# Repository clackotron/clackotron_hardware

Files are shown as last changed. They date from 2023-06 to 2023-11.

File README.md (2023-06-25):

# Clackotron 2000 - Hardware
This repository contains the hardware for the Clackotron 2000 project, which provides a simple, all-in-one solution for controlling SBB split-flap modules. For more information on the project in general, visit the [docs repository](https://github.com/clackotron/clackotron_docs).

The hardware is based around an ESP32-S3 and designed in KiCAD 7.0. The production files can be used to easily order the latest version of the PCB from a manufacturer. (JLCPCB)

Most notably, the hardware contains:
* 30V DC input and +/-/A/B connector (same as SBB split flap modules).
* Internal power supply for 5V (RS485) and 3.3V (ESP32-S3).
* An ESP32-S3 on which the [firmware](https://github.com/clackotron/clackotron_firmware) and [webinterface](https://github.com/clackotron/clackotron_webinterface) will run.
* A level converter for sending/receiving RS485 from the ESP32-S3.
* An RTC (PCF85263A) and battery for time-keeping while offline.
* Two buttons and a RGB-Led for misc. functionality.

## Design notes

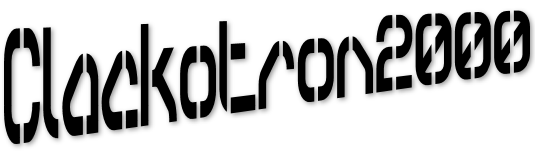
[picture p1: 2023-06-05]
clackotron.png

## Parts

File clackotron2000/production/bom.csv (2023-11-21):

Designator | Footprint | Quantity | Value | LCSC Part #
BT1 | BAT-SMD_MYOUNG_MY-2032-04 | 1 | Battery_Cell | C964837
C1, C10, C12, C13, C15, C3, C4, C6, C7 | 0805 | 9 | 100nF | C49678
C11, C14 | 1206 | 2 | 22uF | C12891
C2, C5, C9 | 0805 | 3 | 1uF | C28323
C8 | CAP-SMD_BD6.3-L6.6-W6.6-LS7.2-FD | 1 | 47uF/35V | C3344
D1 | LED_WS2812B_PLCC4_5.0x5.0mm_P3.2mm | 1 | WS2812B | C2761795
D2, D3, D5 | SOD-523_L1.2-W0.8-LS1.6-BI | 3 | LESD5D5.0CT1G | C383211
D4, D7 | D_SMA | 2 | 1N4007 | C2909831
D6 | 0805 | 1 | LED | C84256
J2 | TerminalBlock_4Ucon_1x02_P3.50mm_Horizontal | 1 | Power | C466970
J3 | TerminalBlock_4Ucon_1x04_P3.50mm_Horizontal | 1 | Output | C98769
Q1, Q2, Q3, Q4 | SOT-23 | 4 | BSN20 | C116157
R1, R10, R15, R16, R17, R18, R2, R3, R4, R7 | 0805 | 10 | 10k | C17414
R11, R12, R13, R14 | 0805 | 4 | 2k2 | C17520
R5, R6 | 0805 | 2 | 5.1k | C17414
R8 | 1206 | 1 | 220R | C17957
R9 | 0805 | 1 | 1k1 | C17375
SW1, SW2 | KEY-SMD_4P-L6.0-W6.0-P4.50-LS9.5-BL | 2 | K2-1102SP-C4SC-04 | C127509
U1 | TSSOP-8_3x3mm_P0.65mm | 1 | PCF85263ATT | C2651543
U2 | WIRELM-SMD_ESP32-S3-WROOM-1 | 1 | ESP32-S3-WROOM-1(N8R2) | C2913204
U3 | SOIC-8_3.9x4.9mm_P1.27mm | 1 | SP3485EN | C5279038
U5 | SOT-223-3_TabPin2 | 1 | AMS1117-3.3 | C369933
USBC1 | USB-C-SMD_TYPE-C-USB-17 | 1 | USB3.1C16PFSMT | C167321
Y1 | Crystal_SMD_3215-2Pin_3.2x1.5mm | 1 | Crystal | C515342

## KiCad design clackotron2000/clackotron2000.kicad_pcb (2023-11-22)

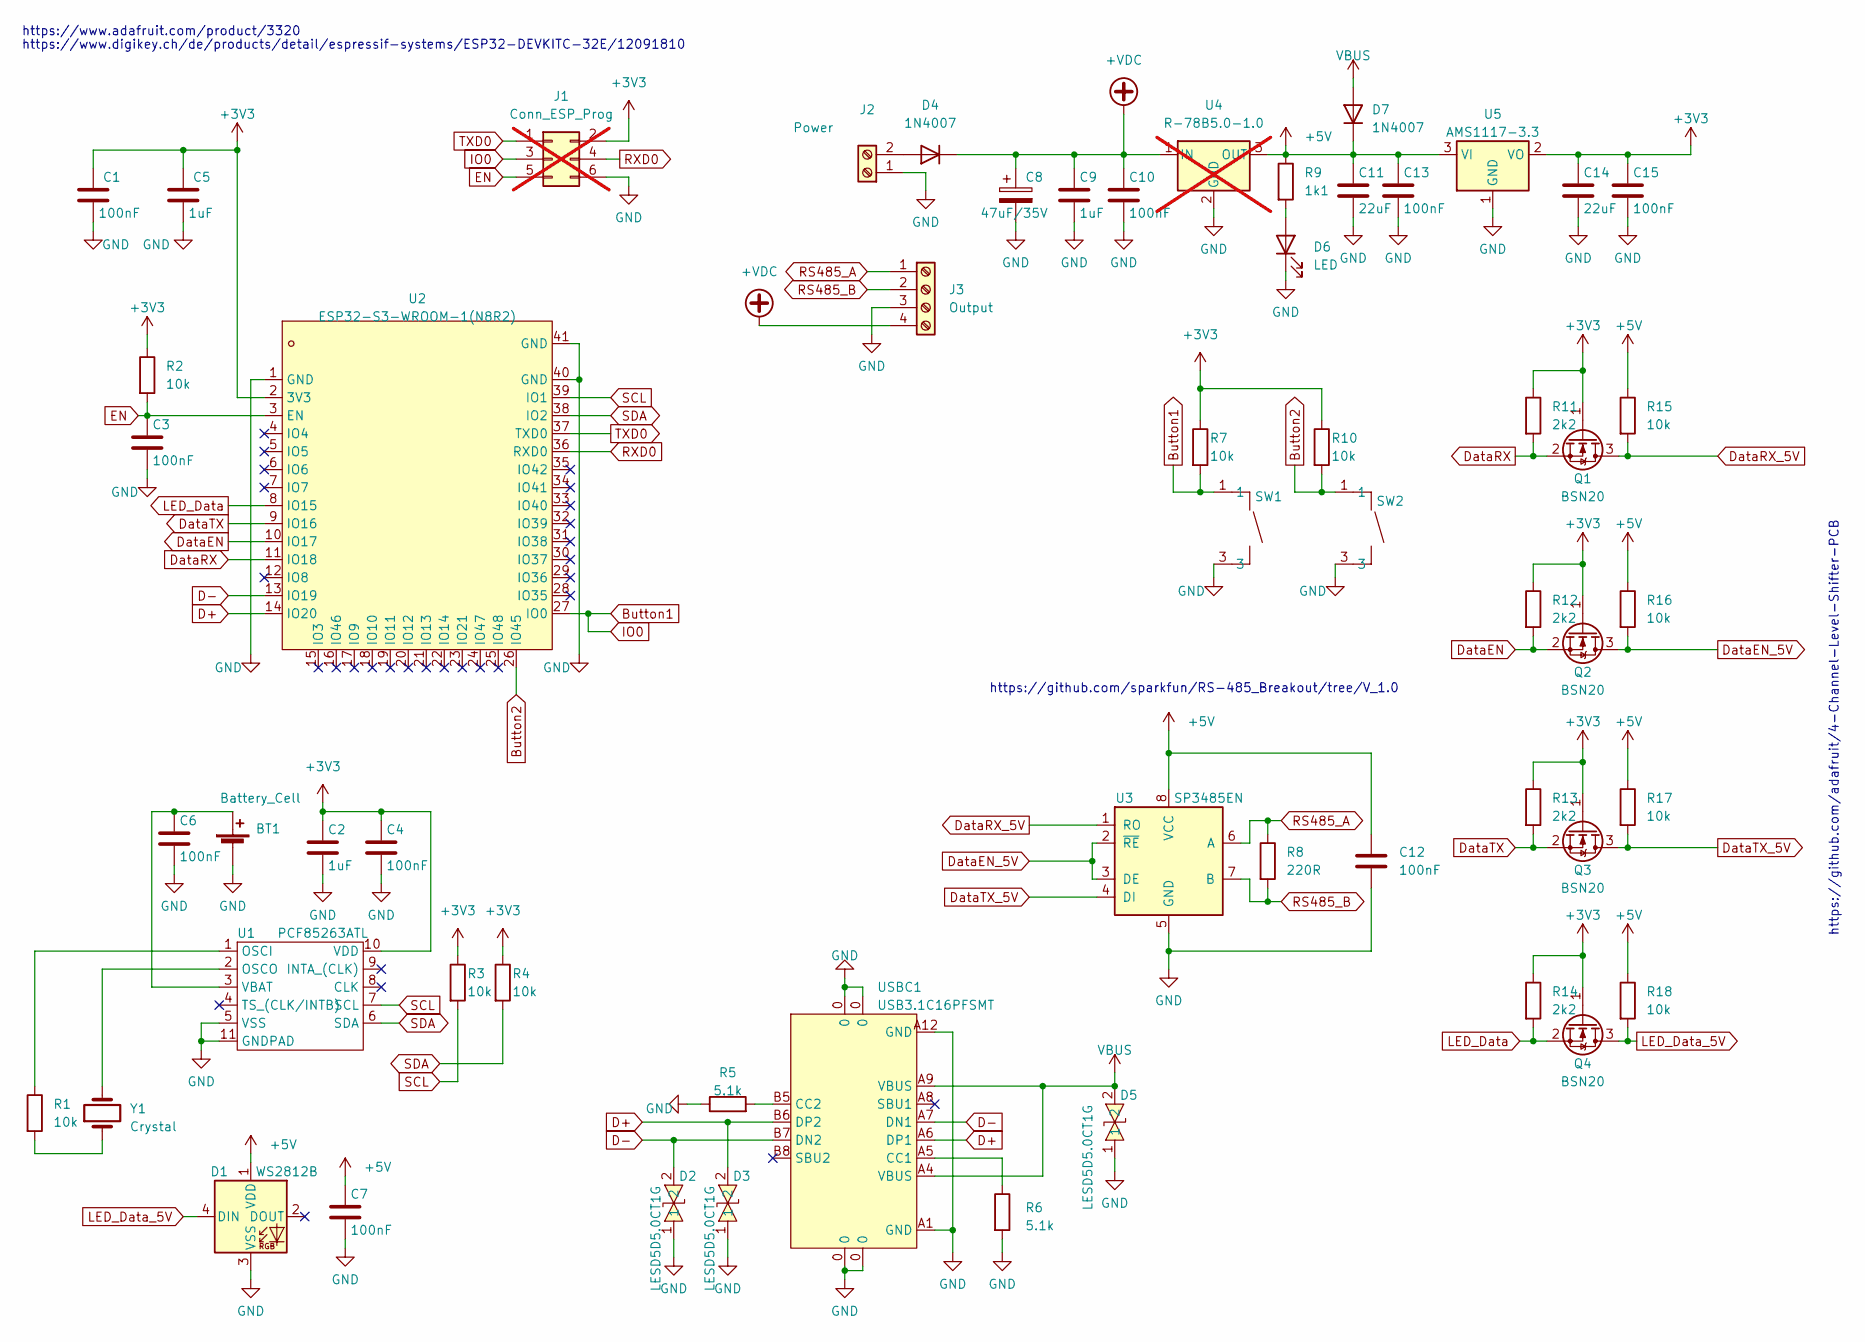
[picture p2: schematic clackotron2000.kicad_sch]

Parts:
BT1: Battery_Cell; BAT-SMD_MYOUNG_MY-2032-04; LCSC Part # C964837
C1, C3, C4, C6, C7, C10, C12, C13, C15: 100nF; C_0805_2012Metric; LCSC Part # C49678
C2, C5, C9: 1uF; C_0805_2012Metric; LCSC Part # C28323
C8: 47uF/35V; CAP-SMD_BD6.3-L6.6-W6.6-LS7.2-FD; LCSC Part # C3344
C11, C14: 22uF; C_1206_3216Metric; LCSC Part # C12891
D1: WS2812B; LED_WS2812B_PLCC4_5.0x5.0mm_P3.2mm; LCSC Part # C2761795
D2, D3, D5: LESD5D5.0CT1G; SOD-523_L1.2-W0.8-LS1.6-BI; LCSC Part C383211
D4, D7: 1N4007; D_SMA; LCSC Part # C2909831
D6: LED; LED_0805_2012Metric; LCSC Part # C84256
J1: Conn_ESP_Prog; PinHeader_2x03_P2.54mm_Vertical; not fitted
J2: Power; TerminalBlock_4Ucon_1x02_P3.50mm_Horizontal; LCSC Part # C466970
J3: Output; TerminalBlock_4Ucon_1x04_P3.50mm_Horizontal; LCSC Part # C98769
Q1, Q2, Q3, Q4: BSN20; SOT-23; LCSC Part # C116157
R1, R2, R3, R4, R7, R10, R15, R16, R17, R18: 10k; R_0805_2012Metric; LCSC Part # C17414
R5, R6: 5.1k; R_0805_2012Metric; LCSC Part # C17414
R8: 220R; R_1206_3216Metric; LCSC Part # C17957
R9: 1k1; R_0805_2012Metric; LCSC Part # C325794
R11, R12, R13, R14: 2k2; R_0805_2012Metric; LCSC Part # C17520
SW1, SW2: K2-1102SP-C4SC-04; KEY-SMD_4P-L6.0-W6.0-P4.50-LS9.5-BL; LCSC Part C127509
U1: PCF85263ATL; DFN-10-1EP_2.6x2.6mm_P0.5mm_EP1.3x2.2mm; LCSC Part C2651523
U2: ESP32-S3-WROOM-1(N8R2); WIRELM-SMD_ESP32-S3-WROOM-1; LCSC Part C2913204
U3: SP3485EN; SOIC-8_3.9x4.9mm_P1.27mm; LCSC Part # C5279038
U4: R-78B5.0-1.0; Converter_DCDC_RECOM_R-78E-0.5_THT; digikey 945-R-78K5.0-1.0-ND; not fitted
U5: AMS1117-3.3; SOT-223-3_TabPin2; LCSC Part # C369933
USBC1: USB3.1C16PFSMT; USB-C-SMD_TYPE-C-USB-17; LCSC Part C167321
Y1: Crystal; Crystal_SMD_3215-2Pin_3.2x1.5mm; LCSC Part # C130253

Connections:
+3V3: C1.1, C2.1, C4.1, C5.1, C14.1, C15.1, J1.2, Q1.1 (G), Q2.1 (G), Q3.1 (G), Q4.1 (G), R2.1, R3.1, R4.1, R7.1, R10.1, R11.1, R12.1, R13.1, R14.1, U1.10 (VDD), U2.2 (3V3), U5.2 (VO)
+5V: C7.1, C11.1, C12.1, C13.1, D1.1 (VDD), D7.1 (K), R9.1, R15.1, R16.1, R17.1, R18.1, U3.8 (VCC), U4.3 (OUT), U5.3 (VI)
+VDC: C8.1, C9.1, C10.1, D4.1 (K), J3.4, U4.1 (IN)
Button1: J1.3, R7.2, SW1.1, SW1.2, U2.27 (IO0)
Button2: R10.2, SW2.1, SW2.2, U2.26 (IO45)
D+: D3.2, U2.14 (IO20), USBC1.A6 (DP1), USBC1.B6 (DP2)
D-: D2.2, U2.13 (IO19), USBC1.A7 (DN1), USBC1.B7 (DN2)
DataEN: Q2.2 (S), R12.2, U2.10 (IO17)
DataEN_5V: Q2.3 (D), R16.2, U3.2 (~RE), U3.3 (DE)
DataRX: Q1.2 (S), R11.2, U2.11 (IO18)
DataRX_5V: Q1.3 (D), R15.2, U3.1 (RO)
DataTX: Q3.2 (S), R13.2, U2.9 (IO16)
DataTX_5V: Q3.3 (D), R17.2, U3.4 (DI)
EN: C3.1, J1.5, R2.2, U2.3 (EN)
GND: BT1.2 (-), C1.2, C2.2, C3.2, C4.2, C5.2, C6.2, C7.2, C8.2, C9.2, C10.2, C11.2, C12.2, C13.2, C14.2, C15.2, D1.3 (VSS), D2.1, D3.1, D5.1, D6.1 (K), J1.6, J2.1, J3.3, R5.1, R6.2, SW1.3, SW1.4, SW2.3, SW2.4, U1.5 (VSS), U1.11 (GNDPAD), U2.1 (GND), U2.40 (GND), U2.41 (GND), U3.5 (GND), U4.2 (GND), U5.1 (GND), USBC1.0, USBC1.A1 (GND), USBC1.A12 (GND)
LED_Data: Q4.2 (S), R14.2, U2.8 (IO15)
LED_Data_5V: D1.4 (DIN), Q4.3 (D), R18.2
unnamed: BT1.1 (+), C6.1, U1.3 (VBAT)
unnamed: D4.2 (A), J2.2
unnamed: D6.2 (A), R9.2
unnamed: R1.2, Y1.1
unnamed: R1.1, U1.1 (OSCI)
unnamed: U1.2 (OSCO), Y1.2
unnamed: R6.1, USBC1.A5 (CC1)
unnamed: R5.2, USBC1.B5 (CC2)
RS485_A: J3.1, R8.1, U3.6 (A)
RS485_B: J3.2, R8.2, U3.7 (B)
RXD0: J1.4, U2.36 (RXD0)
SCL: R3.2, U1.7 (SCL), U2.39 (IO1)
SDA: R4.2, U1.6 (SDA), U2.38 (IO2)
TXD0: J1.1, U2.37 (TXD0)
VBUS: D5.2, D7.2 (A), USBC1.A4 (VBUS), USBC1.A9 (VBUS)

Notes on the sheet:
https://github.com/sparkfun/RS-485_Breakout/tree/V_1.0
https://github.com/adafruit/4-Channel-Level-Shifter-PCB
https://www.adafruit.com/product/3320
https://www.digikey.ch/de/products/detail/espressif-systems/ESP32-DEVKITC-32E/12091810

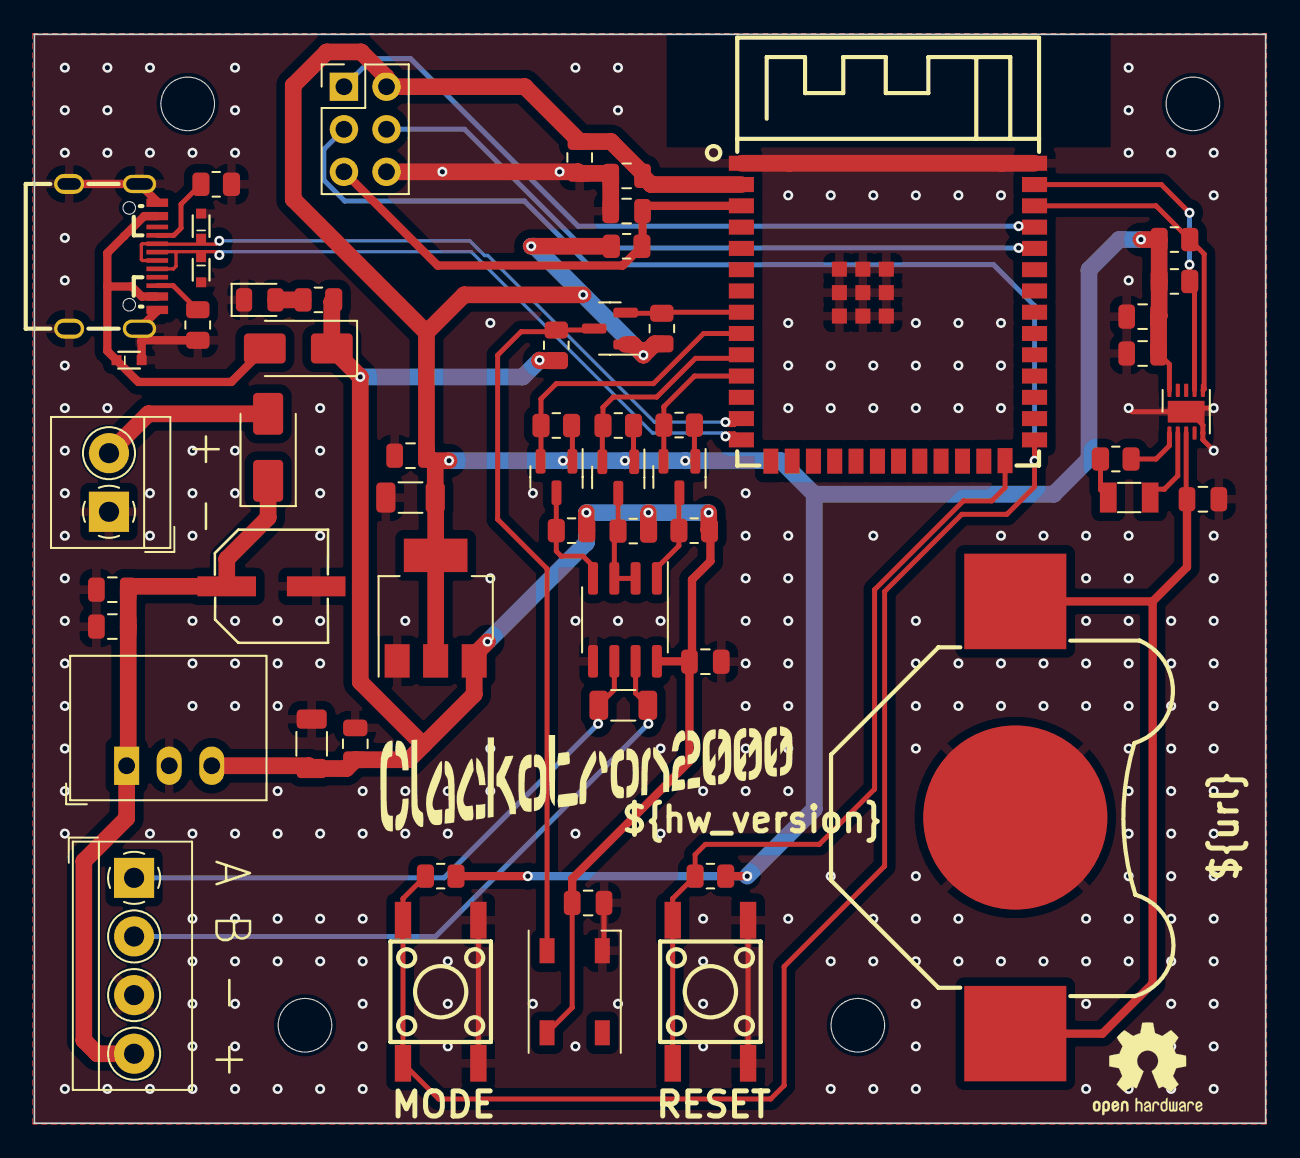
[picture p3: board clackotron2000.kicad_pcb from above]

Board: 2 copper layers, 73.5 x 65.0 mm, 57 parts (0 on the bottom side), 32 nets.

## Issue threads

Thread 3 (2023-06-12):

remove ws2812 led's

mburger82, 2023-06-12:
nescessary?

mburger82, 2023-06-13:
1 WS2812 LED instead of all other LED's is enough

cybrox, 2023-06-13:
Quickly tested, HW works with current wiring

```cpp
CRGB leds[1];
void setup() {
    // FastLED.addLeds<NEOPIXEL, 6>(leds, 1);
    FastLED.addLeds<WS2812, 23, GRB>(leds, 1);
}

void loop() {
    leds[0] = CRGB::Red; FastLED.show(); delay(5);
    leds[0] = CRGB::Black; FastLED.show(); delay(5);
}

```

mburger82, 2023-06-25:
dscision to keep it

Closed 2023-06-25.

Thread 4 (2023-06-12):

remove 1 button

mburger82, 2023-06-12:
1 Button should be enough

mburger82, 2023-06-13:
No,
Keep both.
Name them Mode and Reset

mburger82, 2023-06-25:
descision against it

Closed 2023-06-25.

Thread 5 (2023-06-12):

remove 1 simple led.

mburger82, 2023-06-12:
1 signalling led is enough?

mburger82, 2023-06-13:
remove both simple led's.
Power Led is staying

mburger82, 2023-06-25:
done 090c3b0f98891dc94b6d2d937f73e9f70ca1602d

Closed 2023-06-25.

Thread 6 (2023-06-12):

add mounting holes

mburger82, 2023-06-12:
mounting holes went missing somewhere between v1.0 and v2.0

mburger82, 2023-06-12:
maybe also find bether positions...

mburger82, 2023-06-25:
done 090c3b0f98891dc94b6d2d937f73e9f70ca1602d

Closed 2023-06-25.

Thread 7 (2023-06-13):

Change ESP32 to ESP32-S3 for USB Programming Capabilities

mburger82, 2023-06-13:
User Button on IO0 for emergency programming procedure

mburger82, 2023-06-25:
done 090c3b0f98891dc94b6d2d937f73e9f70ca1602d

Closed 2023-06-25.

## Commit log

2023-06-12 chore: rebase changes from internal repository
    [clackotron2000.kicad_pcb, clackotron2000.kicad_sch]
2023-06-13 add new parts for next hardware revision to schematic
    [clackotron2000.kicad_sch]
2023-06-14 hardware redesign for v3.0 done
    [clackotron2000.kicad_pcb, clackotron2000.kicad_sch]
2023-06-20 generate production data and fix some part numbers and stuff
    [clackotron2000.kicad_pcb, clackotron2000.kicad_sch]
2023-06-25 add oshw logo and fix some pcb part configs
    [clackotron2000.kicad_pcb]
2023-06-25 change gitignore to include all production files!
    [bom.csv, designators.csv, positions.csv]
2023-11-21 add new parts. not yet done...
    [bom.csv, clackotron2000.kicad_sch]
2023-11-22 changed all parts. set to version 3.1
    [bom.csv, clackotron2000.kicad_pcb, clackotron2000.kicad_sch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]
2026-01-21 improve voltage safety margins of outputs
    - change rs485 transceiver to other model (successor of the one used in the original splitflap board)
    - add tvs diodes to rs485 lines
    - add series resistors to rs485 lines
